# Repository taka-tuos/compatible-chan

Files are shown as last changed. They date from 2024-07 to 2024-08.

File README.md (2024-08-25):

# compatible-chan
[スタックチャン](https://github.com/stack-chan/stack-chan) 用の自由なCoreモジュール (GPLv3)

# ・ _ ・
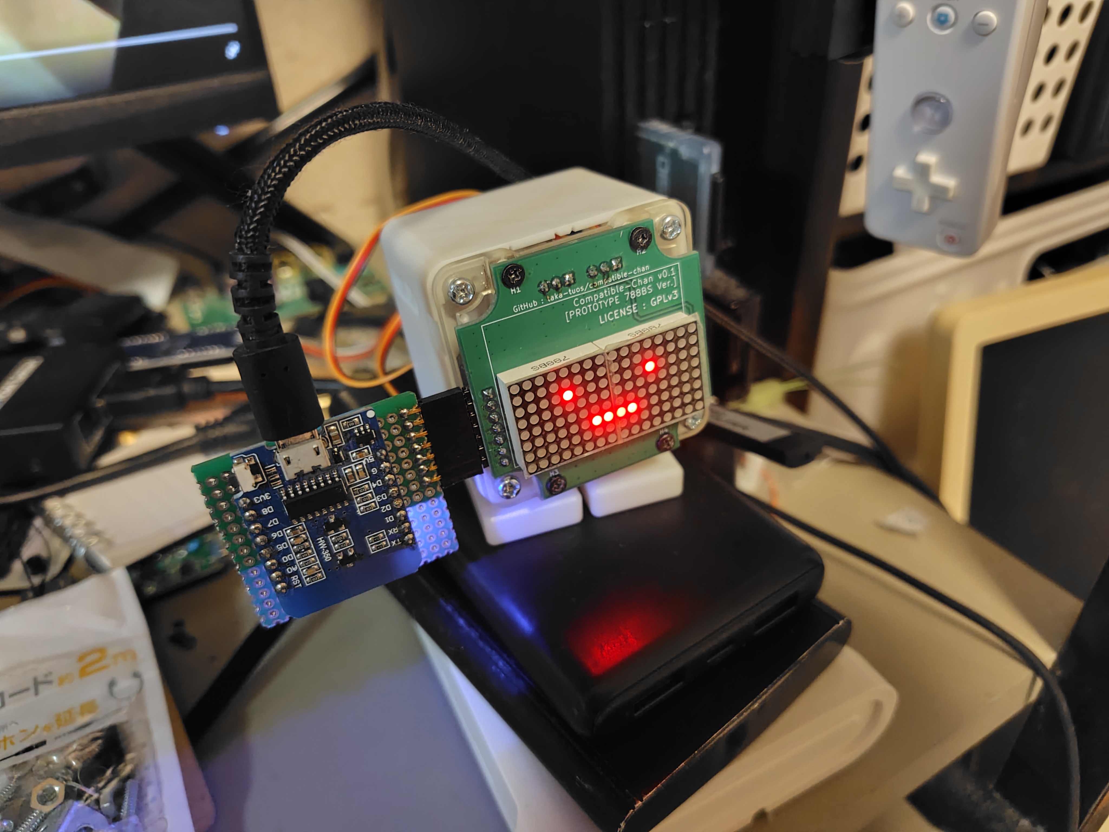
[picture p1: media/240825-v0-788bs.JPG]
v0.1-led 788bs版の動作の様子


# このプロジェクトのスコープ
- スタックチャンのCoreモジュールに自由な選択肢を追加することが目的
- M5Stack系の製品を広範に置き換えるもの**ではない** (スタックチャンに必要な機能のみを実装する)

# FAQ
## Q. M5Stackって「オープンハードウェア」では？
A. 各種ピン仕様や回路図こそオープンではあるが、シェルのCADデータやガーバーファイル、BOM等が公開されていないので「自由」ではない(と自分は考えている)。

## Q. 自由でないと何がダメ？
A. スタックチャンは「サ終とともに死ぬロボットはアカン(意訳)」という思想を含んでいて[^1](https://protopedia.net/prototype/2345)、M5Stackの供給が止まると死ぬ状況はよろしくないはず。  
(実際オンラインに依存していない旧AIBOシリーズでも、部品供給が無いのでバタバタ死んでいる)  
またM5Stackの仕様に縛られる状況でその打開ができないのもよろしくない(よく挙がる例としてはスピーカーとマイクが排他なことなど)

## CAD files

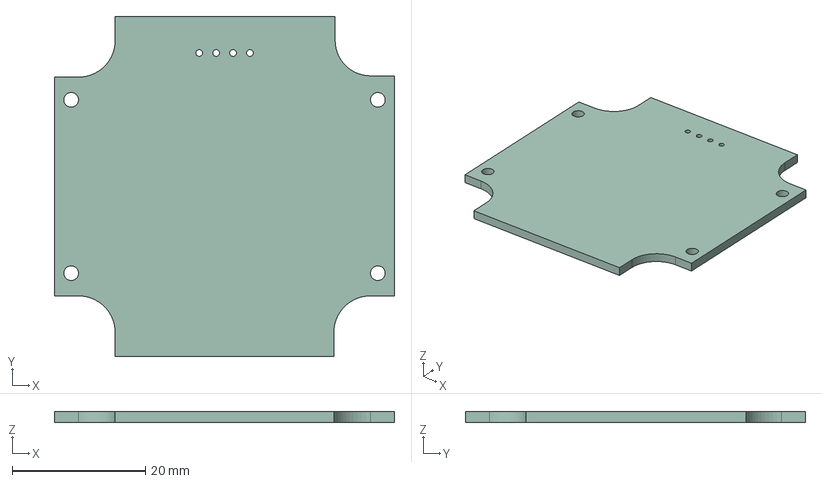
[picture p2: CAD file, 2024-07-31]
compatible-chan-v0/compatible-chan-v0.step
51.0 x 51.0 x 1.60 mm

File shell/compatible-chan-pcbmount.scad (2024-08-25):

use <pcb.scad>

$fn = $preview ? 16 : 48;
m_led = true;

module roundsquare(s, r) {
    union() {
        square(s-r*2, true);
        translate([-(s/2-r),-(s/2-r), 0]) circle(r);
        translate([ (s/2-r),-(s/2-r), 0]) circle(r);
        translate([-(s/2-r), (s/2-r), 0]) circle(r);
        translate([ (s/2-r), (s/2-r), 0]) circle(r);
        translate([-(s/2-r), 0, 0]) square([r*2, s-r*2], true);
        translate([ (s/2-r), 0, 0]) square([r*2, s-r*2], true);
        translate([0,-(s/2-r), 0]) square([s-r*2, r*2], true);
        translate([0, (s/2-r), 0]) square([s-r*2, r*2], true);
    }
}

module outershell(s, r, t, h) {
    linear_extrude(h, convexity = 2) {
        difference() {
            roundsquare(s, r);
            roundsquare(s - t, r - t/2);
        }
    }
}

module screwstand(r1, r2, h, d, b1 = 0, b2 = 0, b3 = 0, b4 = 0) {
    union(){
        linear_extrude(h, convexity = 2) {
            difference() {
                circle(r2);
                circle(r1);
            }
        }
        cylinder(h - d, r2, r2);
        
        difference() {
            union() {
                if(b1 == 1) {
                    translate([-(r2/2), -(r2/2), h / 2]) cube([r2, r2, h], true);
                }
                
                if(b2 == 1) {
                    translate([-(r2/2),  (r2/2), h / 2]) cube([r2, r2, h], true);
                }
                
                if(b3 == 1) {
                    translate([ (r2/2), -(r2/2), h / 2]) cube([r2, r2, h], true);
                }
                
                if(b4 == 1) {
                    translate([ (r2/2),  (r2/2), h / 2]) cube([r2, r2, h], true);
                }
            }
            translate([0, 0, -1]) cylinder(h + 2, r2, r2);
        }
    }
}

union() {
    translate([-(27-5.1),-(27-5.1), 0]) screwstand(2.0, 4.6, 3, 5, 0, 1, 1, 0); 
    translate([-(27-5.1), (27-5.1), 0]) screwstand(2.0, 4.6, 3, 5, 1, 0, 0, 1); 
    translate([ (27-5.1),-(27-5.1), 0]) screwstand(2.0, 4.6, 3, 5, 1, 0, 0, 1); 
    translate([ (27-5.1), (27-5.1), 0]) screwstand(2.0, 4.6, 3, 5, 0, 1, 1, 0); 
    
    translate([-13, -(27-4), 0]) screwstand(1.75, 3.5, 6, 8, 1, 1, 0, 0);
    translate([-13,  (27-4), 0]) screwstand(1.75, 3.5, 6, 8, 1, 1, 0, 0);
    translate([ 13, -(27-4), 0]) screwstand(1.75, 3.5, 6, 8, 0, 0, 1, 1);
    translate([ 13,  (27-4), 0]) screwstand(1.75, 3.5, 6, 8, 0, 0, 1, 1);
    
    linear_extrude(3, convexity = 2) {
        translate([0, -(27-4)]) square([22, 3],true);
        translate([0,  (27-4)]) square([22, 3],true);
        
        translate([-(27-2), 0]) square([3, 35],true);
        translate([ (27-2), 0]) square([3, 35],true);
        
        translate([-(27-9), -(27-4)]) square([3, 7],true);
        translate([-(27-9),  (27-4)]) square([3, 7],true);
        translate([ (27-9), -(27-4)]) square([3, 7],true);
        translate([ (27-9),  (27-4)]) square([3, 7],true);
    }
}

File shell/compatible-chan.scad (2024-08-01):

use <pcb.scad>

$fn = $preview ? 16 : 48;
m_led = true;

module roundsquare(s, r) {
    union() {
        square(s-r*2, true);
        translate([-(s/2-r),-(s/2-r), 0]) circle(r);
        translate([ (s/2-r),-(s/2-r), 0]) circle(r);
        translate([-(s/2-r), (s/2-r), 0]) circle(r);
        translate([ (s/2-r), (s/2-r), 0]) circle(r);
        translate([-(s/2-r), 0, 0]) square([r*2, s-r*2], true);
        translate([ (s/2-r), 0, 0]) square([r*2, s-r*2], true);
        translate([0,-(s/2-r), 0]) square([s-r*2, r*2], true);
        translate([0, (s/2-r), 0]) square([s-r*2, r*2], true);
    }
}

module outershell(s, r, t, h) {
    linear_extrude(h, convexity = 2) {
        difference() {
            roundsquare(s, r);
            roundsquare(s - t, r - t/2);
        }
    }
}

module screwstand(r1, r2, h, d, b1 = 0, b2 = 0, b3 = 0, b4 = 0) {
    union(){
        linear_extrude(h, convexity = 2) {
            difference() {
                circle(r2);
                circle(r1);
            }
        }
        cylinder(h - d, r2, r2);
        
        difference() {
            union() {
                if(b1 == 1) {
                    translate([-(r2/2), -(r2/2), h / 2]) cube([r2, r2, h], true);
                }
                
                if(b2 == 1) {
                    translate([-(r2/2),  (r2/2), h / 2]) cube([r2, r2, h], true);
                }
                
                if(b3 == 1) {
                    translate([ (r2/2), -(r2/2), h / 2]) cube([r2, r2, h], true);
                }
                
                if(b4 == 1) {
                    translate([ (r2/2),  (r2/2), h / 2]) cube([r2, r2, h], true);
                }
            }
            translate([0, 0, -1]) cylinder(h + 2, r2, r2);
        }
    }
}

union() {
    difference() {
        outershell(54, 5, 1.8, 13);
        translate([0, 0, 11.5]) {
            difference() {
                outershell(54-1.4, 5-0.7, 1.8, 2.5);
                cube([54-20, 60, 12], true);
                cube([60, 54-15, 12], true);
            }
        }
        if(!m_led) {
            translate([-10, 0, 10]) {
                cube([60, 35, 25], true);
            }
        }
        translate([0, 0, 7.2+5]) {
            cube([60, 35, 10], true);
        }
    }
    
    translate([-(27-5.1),-(27-5.1), 1.5]) screwstand(2.1, 4.5, 9, 5, 0, 1, 1, 0); 
    translate([-(27-5.1), (27-5.1), 1.5]) screwstand(2.1, 4.5, 9, 5, 1, 0, 0, 1); 
    translate([ (27-5.1),-(27-5.1), 1.5]) screwstand(2.1, 4.5, 9, 5, 1, 0, 0, 1); 
    translate([ (27-5.1), (27-5.1), 1.5]) screwstand(2.1, 4.5, 9, 5, 0, 1, 1, 0); 
    
    translate([-13, -(27-4), 1.5]) screwstand(1.75, 3.5, 5.6, 5, 1, 0, 1, 0);
    translate([-13,  (27-4), 1.5]) screwstand(1.75, 3.5, 5.6, 5, 0, 1, 0, 1);
    
    translate([ 13, -(27-4), 1.5]) screwstand(1.75, 3.5, 5.6, 5, 1, 0, 1, 0);
    translate([ 13,  (27-4), 1.5]) screwstand(1.75, 3.5, 5.6, 5, 0, 1, 0, 1);
    
    if(!m_led) {
        translate([47.8 / 2 - 1.7 + 0.5, 0, 1.5 + 0.5]) cube([1, 36, 1], true);
    }
    
    if($preview) {
        /*translate([0, -2, 2.8]) {
            color("SteelBlue") {
                difference() {
                    translate([0, 0, 0.6]) cube([34, 47, 1.2], true);
                    translate([-(29/2), -(42/2), -2]) cylinder(4, 1.1, 1.1);
                    translate([ (29/2), -(42/2), -2]) cylinder(4, 1.1, 1.1);
                    translate([-(29/2),  (42/2), -2]) cylinder(4, 1.1, 1.1);
                    translate([ (29/2),  (42/2), -2]) cylinder(4, 1.1, 1.1);
                }
            }
            
            color("DarkGray") {
                translate([0, 2.819, -0.75]) cube([28.86, 28.86, 1.8], true);
            }
            
            color("DimGray") {
                translate([0, 0.5, -0.7]) cube([33.9, 37.3, 1.7], true);
            }
            
            color("DimGray") {
                translate([0, 22, 2.54]) cube([10.16, 2.54, 2.54], true);
            }
            
            color("Gold") {
                translate([-1.27     , 22, -1.8+6]) cube([0.6, 0.6, 1.8+1.2+2.54+6], true);
                translate([-1.27-2.54, 22, -1.8+6]) cube([0.6, 0.6, 1.8+1.2+2.54+6], true);
                translate([ 1.27     , 22, -1.8+6]) cube([0.6, 0.6, 1.8+1.2+2.54+6], true);
                translate([ 1.27+2.54, 22, -1.8+6]) cube([0.6, 0.6, 1.8+1.2+2.54+6], true);
            }
        }*/
        
        if(!m_led) {
            translate([-1.7, 0, 1.05 + 1.5]) {
                color("Silver") {
                    translate([0, 0, 0]) cube([47.8, 34.6, 2.05], true);
                }
                
                color("DimGray") {
                    translate([1.7, 0, -0.1]) cube([40.8, 30.6, 2.0], true);
                }
            }
        } else {
            //color("Gray", 0.2) {
                translate([0, 0, 6.6 + 1.6]) {
                    rotate([0, 180, 0]) {
                        //import("compatible-chan-v0-led.stl", convexity = 2);
                        //TXFM_1();
                    }
                }
            //}
        }
    }
    
    //color("DimGray", 0.6) {
        difference() {
            translate([0, 0, 0.3]) linear_extrude(1.2, convexity = 2) roundsquare(54-0.9, 5-0.45);
            if(!m_led) {
                cube([40.8, 30.6, 4], true);
            } else {
                translate([0, -4.6, 0]) cube([41, 20.5, 4], true);
            }
            
            //cube([27.972, 32.634, 4], true);
            //translate([0, 2.819-2, 0]) cube([28.86, 28.86, 4], true);
            //translate([0, 2, 0]) cylinder(4, 16, 16);
            //translate([0, 0, 1.5]) cube([42.04, 27.22, 1.0], true);
        }
    //}
}

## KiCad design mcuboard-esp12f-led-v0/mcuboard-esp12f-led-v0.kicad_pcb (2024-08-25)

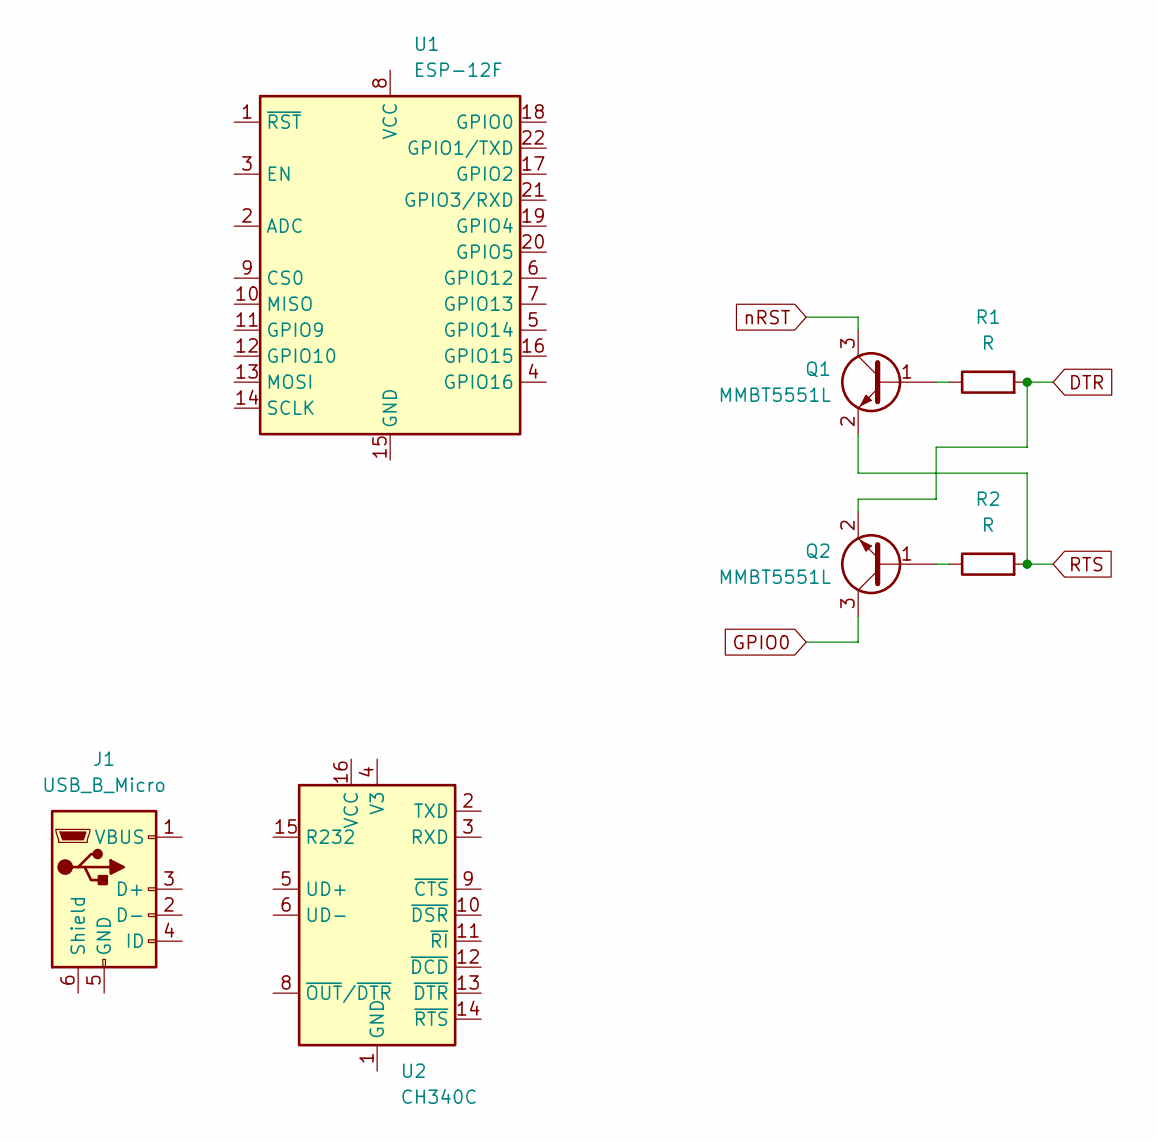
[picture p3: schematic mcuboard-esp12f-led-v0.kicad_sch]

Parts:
J1: USB_B_Micro; USB_Micro-B_Wuerth_629105150521
Q1, Q2: MMBT5551L; SOT-23
R1, R2: R; R_0805_2012Metric_Pad1.20x1.40mm_HandSolder
U1: ESP-12F; ESP-12E
U2: CH340C; SOIC-16_3.9x9.9mm_P1.27mm

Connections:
DTR: Q2.2 (E), R1.2
GPIO0: Q2.3 (C)
unnamed: Q1.1 (B), R1.1
unnamed: Q2.1 (B), R2.1
RTS: Q1.2 (E), R2.2
nRST: Q1.3 (C)

Board: 2 copper layers, 7 parts (0 on the bottom side), 4 nets, no tracks yet.

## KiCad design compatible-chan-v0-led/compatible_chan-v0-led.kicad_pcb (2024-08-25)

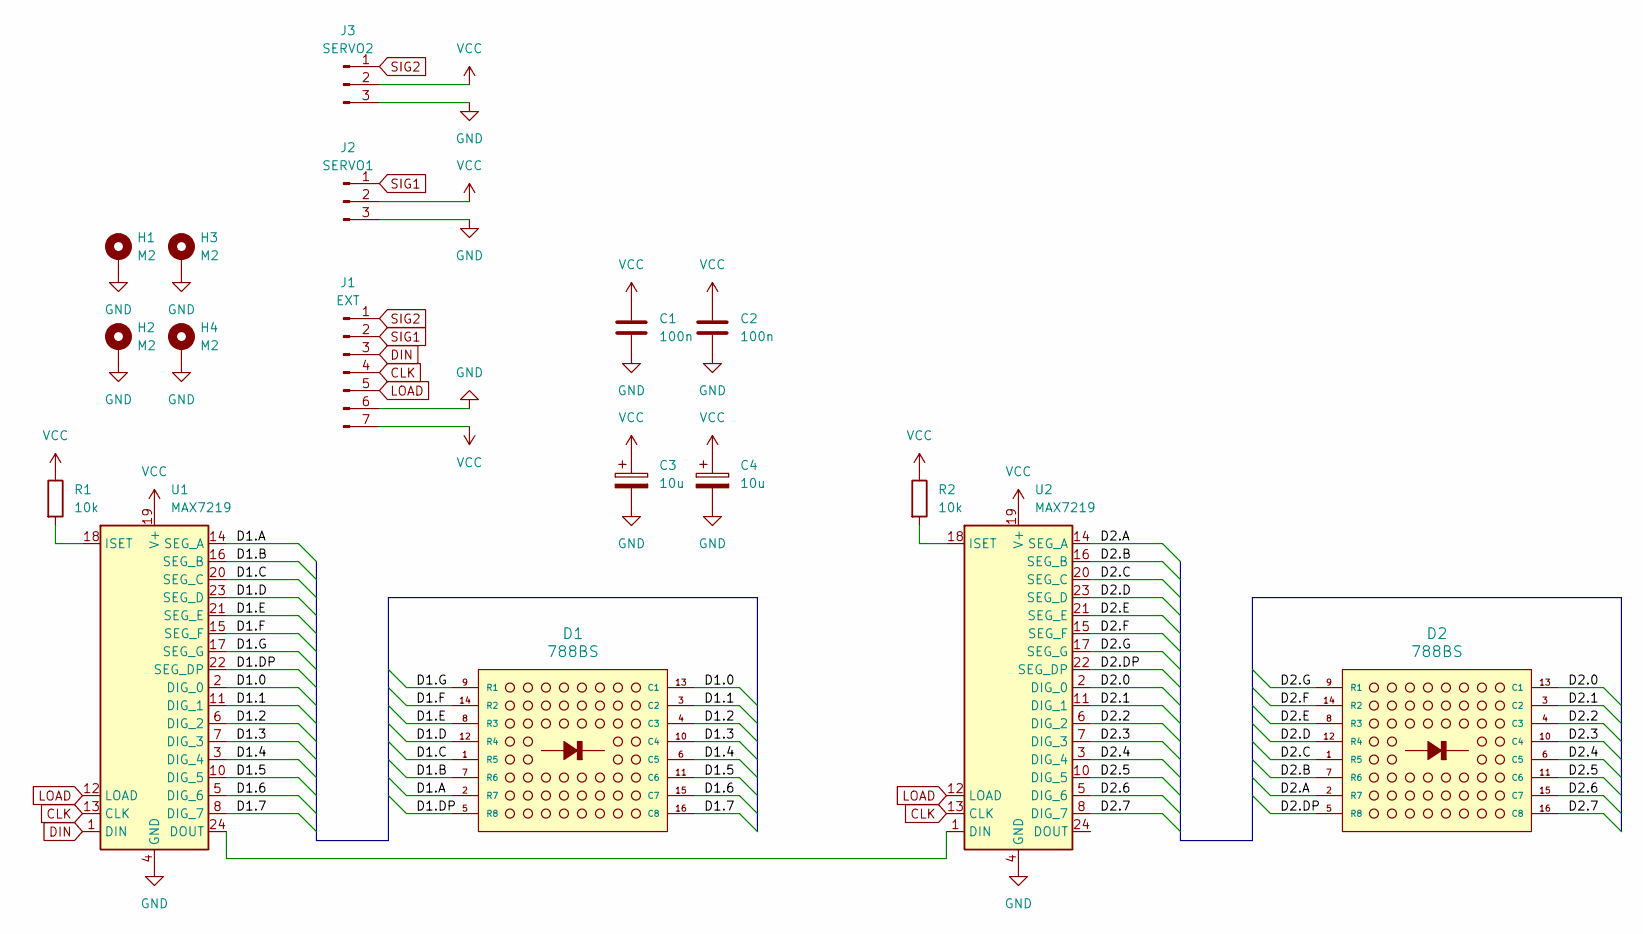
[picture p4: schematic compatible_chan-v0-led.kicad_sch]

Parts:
C1, C2: 100n; C_0805_2012Metric_Pad1.18x1.45mm_HandSolder
C3, C4: 10u; CP_EIA-2012-15_AVX-P_Pad1.30x1.05mm_HandSolder
D1, D2: 788BS; LED_8x8_1.9MM_20x20MM
H1, H2, H3, H4: M2; MountingHole_2.2mm_M2_DIN965_Pad
J1: EXT; PinHeader_1x07_P2.54mm_Horizontal
J2: SERVO1; PinHeader_1x03_P2.54mm_Vertical
J3: SERVO2; PinHeader_1x03_P2.54mm_Vertical
R1, R2: 10k; R_Axial_DIN0207_L6.3mm_D2.5mm_P10.16mm_Horizontal
U1, U2: MAX7219; SOIC-24W_7.5x15.4mm_P1.27mm

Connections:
/D1.0: D1.13 (C1), U1.2 (DIG_0)
/D1.1: D1.3 (C2), U1.11 (DIG_1)
/D1.2: D1.4 (C3), U1.6 (DIG_2)
/D1.3: D1.10 (C4), U1.7 (DIG_3)
/D1.4: D1.6 (C5), U1.3 (DIG_4)
/D1.5: D1.11 (C6), U1.10 (DIG_5)
/D1.6: D1.15 (C7), U1.5 (DIG_6)
/D1.7: D1.16 (C8), U1.8 (DIG_7)
/D1.A: D1.2 (R7), U1.14 (SEG_A)
/D1.B: D1.7 (R6), U1.16 (SEG_B)
/D1.C: D1.1 (R5), U1.20 (SEG_C)
/D1.D: D1.12 (R4), U1.23 (SEG_D)
/D1.DP: D1.5 (R8), U1.22 (SEG_DP)
/D1.E: D1.8 (R3), U1.21 (SEG_E)
/D1.F: D1.14 (R2), U1.15 (SEG_F)
/D1.G: D1.9 (R1), U1.17 (SEG_G)
/D2.0: D2.13 (C1), U2.2 (DIG_0)
/D2.1: D2.3 (C2), U2.11 (DIG_1)
/D2.2: D2.4 (C3), U2.6 (DIG_2)
/D2.3: D2.10 (C4), U2.7 (DIG_3)
/D2.4: D2.6 (C5), U2.3 (DIG_4)
/D2.5: D2.11 (C6), U2.10 (DIG_5)
/D2.6: D2.15 (C7), U2.5 (DIG_6)
/D2.7: D2.16 (C8), U2.8 (DIG_7)
/D2.A: D2.2 (R7), U2.14 (SEG_A)
/D2.B: D2.7 (R6), U2.16 (SEG_B)
/D2.C: D2.1 (R5), U2.20 (SEG_C)
/D2.D: D2.12 (R4), U2.23 (SEG_D)
/D2.DP: D2.5 (R8), U2.22 (SEG_DP)
/D2.E: D2.8 (R3), U2.21 (SEG_E)
/D2.F: D2.14 (R2), U2.15 (SEG_F)
/D2.G: D2.9 (R1), U2.17 (SEG_G)
CLK: J1.4, U1.13 (CLK), U2.13 (CLK)
DIN: J1.3, U1.1 (DIN)
GND: C1.2, C2.2, C3.2, C4.2, H1.1, H2.1, H3.1, H4.1, J1.6, J2.3, J3.3, U1.4 (GND), U1.9 (GND), U2.4 (GND), U2.9 (GND)
LOAD: J1.5, U1.12 (LOAD), U2.12 (LOAD)
unnamed: U1.24 (DOUT), U2.1 (DIN)
unnamed: R1.2, U1.18 (ISET)
unnamed: R2.2, U2.18 (ISET)
SIG1: J1.2, J2.1
SIG2: J1.1, J3.1
VCC: C1.1, C2.1, C3.1, C4.1, J1.7, J2.2, J3.2, R1.1, R2.1, U1.19 (V+), U2.19 (V+)

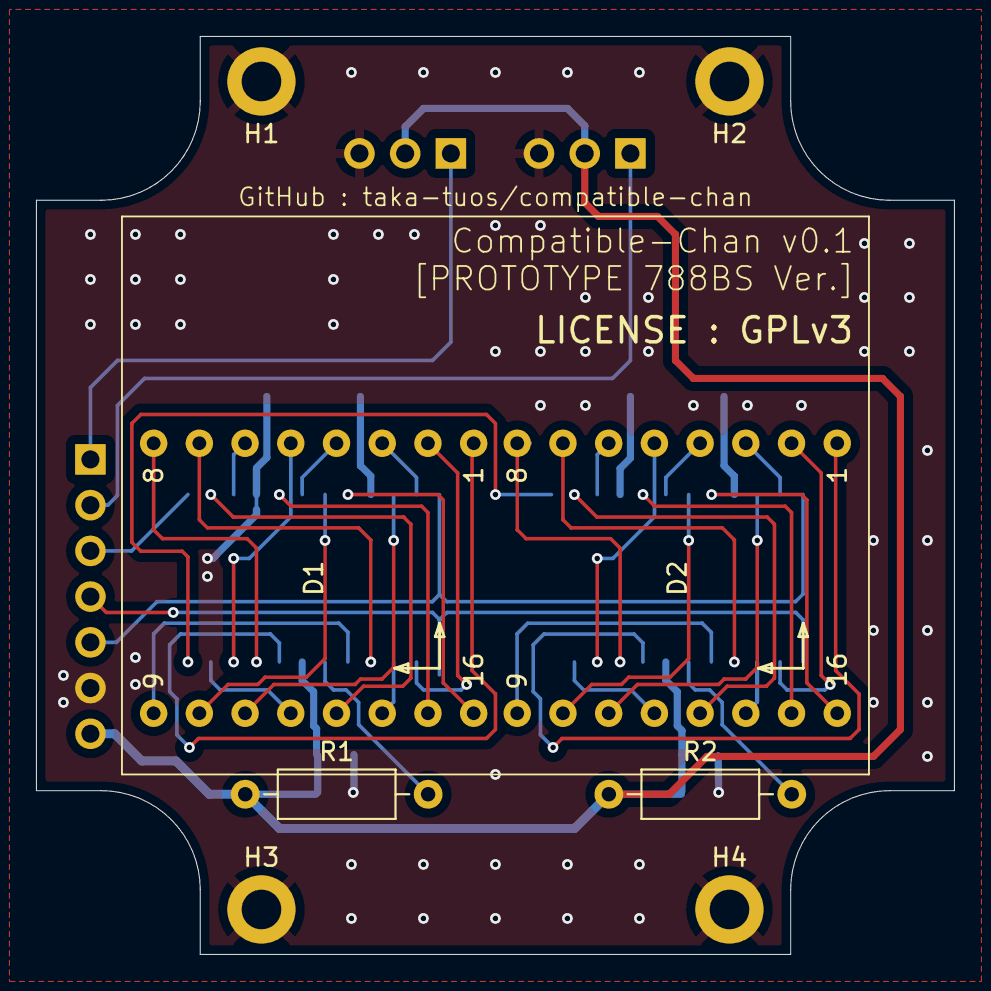
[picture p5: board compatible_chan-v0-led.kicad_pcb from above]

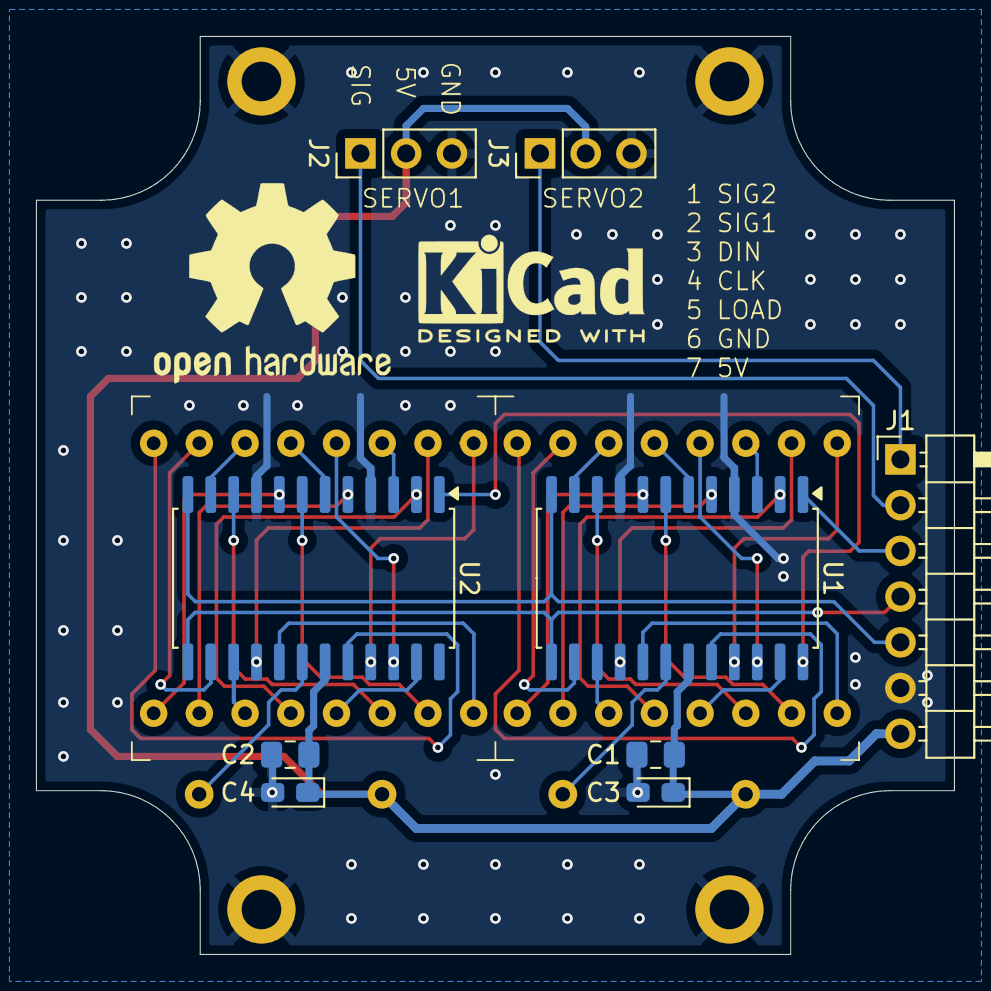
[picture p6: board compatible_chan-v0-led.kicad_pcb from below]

Board: 2 copper layers, 51.0 x 51.0 mm, 17 parts (9 on the bottom side), 42 nets.

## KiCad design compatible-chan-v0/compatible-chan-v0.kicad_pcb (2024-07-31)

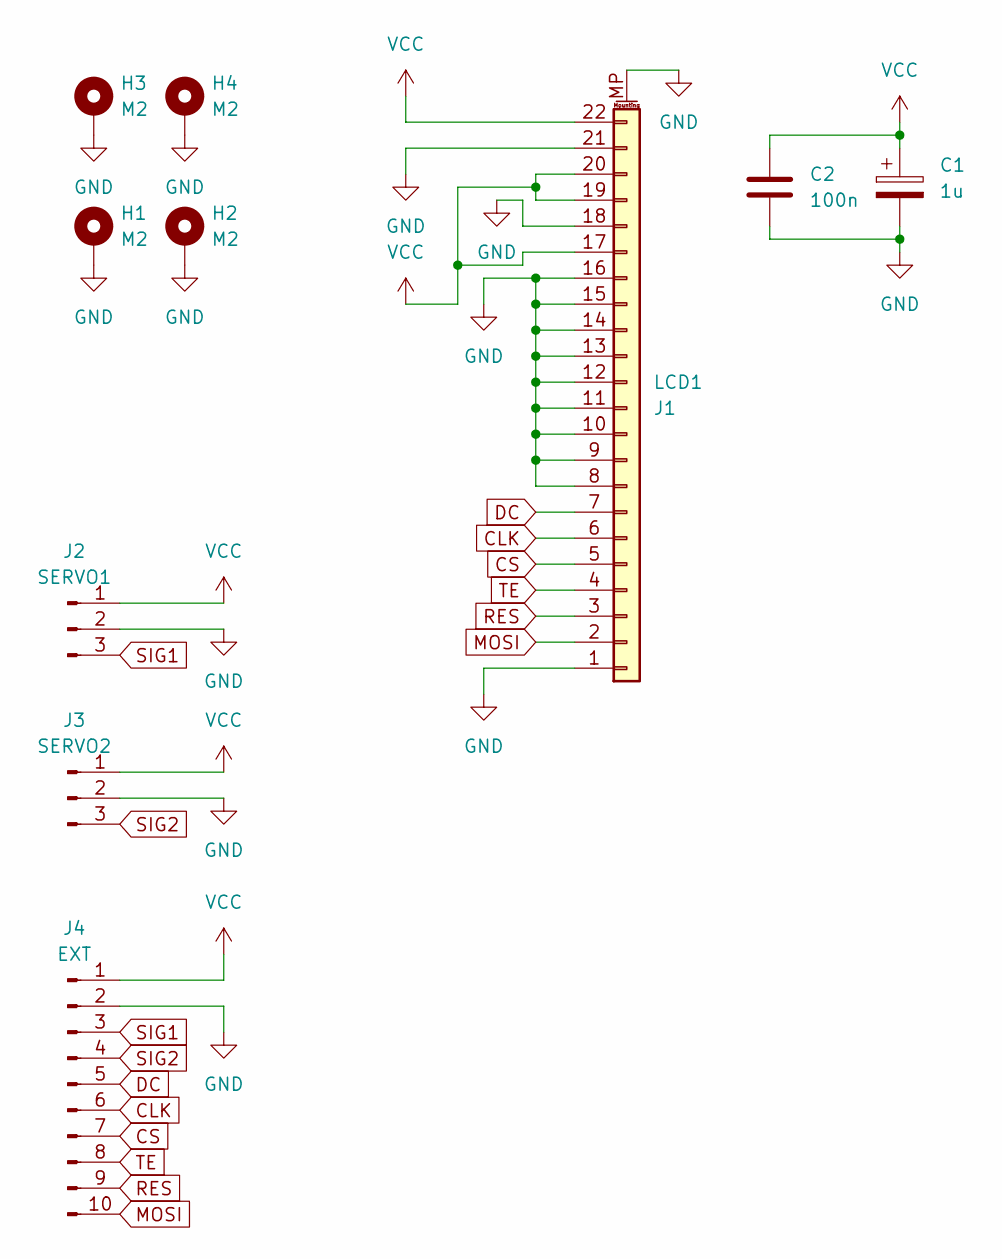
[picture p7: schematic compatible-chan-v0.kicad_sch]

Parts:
C1: 1u; CP_EIA-2012-12_Kemet-R_Pad1.30x1.05mm_HandSolder
C2: 100n; C_0805_2012Metric_Pad1.18x1.45mm_HandSolder
H1, H2, H3, H4: M2; MountingHole_2.2mm_M2_DIN965_Pad
J1: LCD1; TE_2-1734839-2_1x22-1MP_P0.5mm_Horizontal
J2: SERVO1; PinHeader_1x03_P2.54mm_Vertical
J3: SERVO2; PinHeader_1x03_P2.54mm_Vertical
J4: EXT; PinHeader_1x10_P2.54mm_Horizontal

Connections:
CLK: J1.6, J4.6
CS: J1.5, J4.7
DC: J1.7, J4.5
GND: C1.2, C2.2, H1.1, H2.1, H3.1, H4.1, J1.1, J1.8, J1.9, J1.10, J1.11, J1.12, J1.13, J1.14, J1.15, J1.16, J1.18, J1.21, J1.MP (MountPin), J2.2, J3.2, J4.2
MOSI: J1.2, J4.10
RES: J1.3, J4.9
SIG1: J2.3, J4.3
SIG2: J3.3, J4.4
TE: J1.4, J4.8
VCC: C1.1, C2.1, J1.17, J1.19, J1.20, J1.22, J2.1, J3.1, J4.1

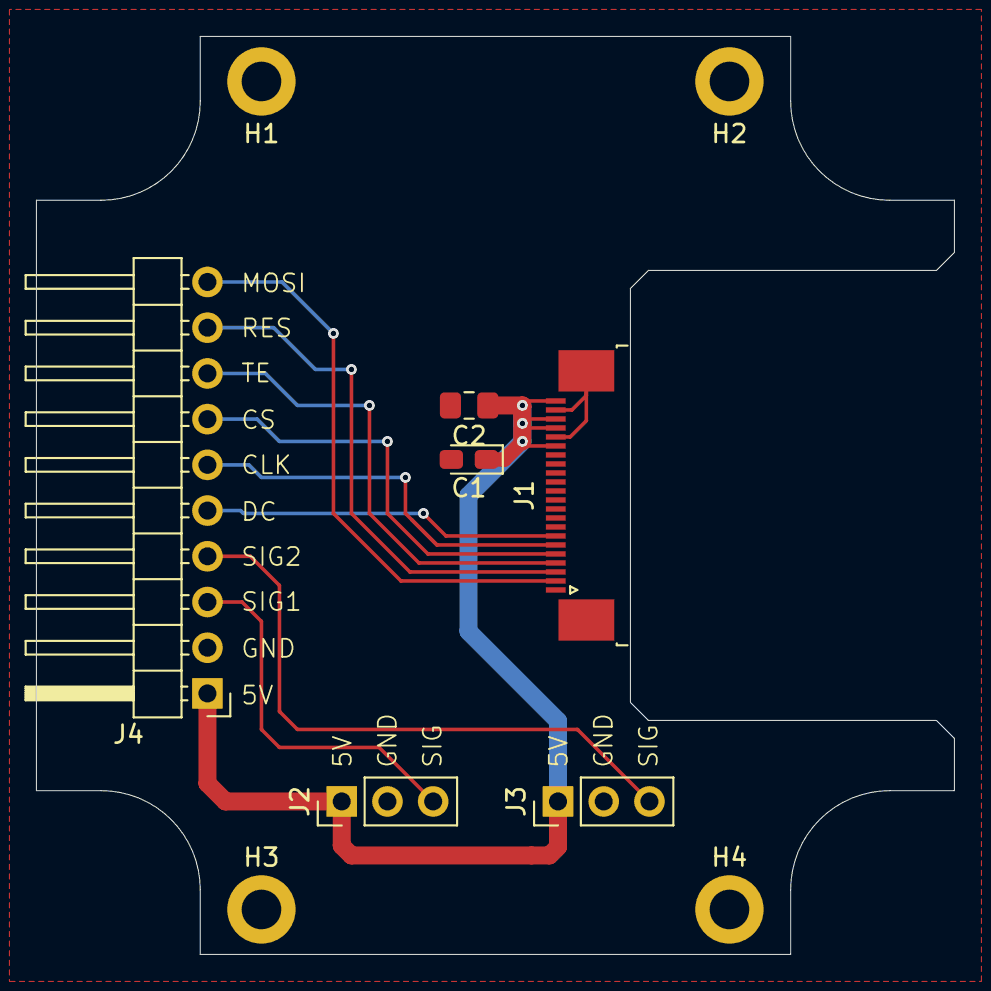
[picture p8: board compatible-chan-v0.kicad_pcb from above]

Board: 2 copper layers, 51.0 x 51.0 mm, 10 parts (0 on the bottom side), 10 nets.

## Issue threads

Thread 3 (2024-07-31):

v0 - 外装

taka-tuos, 2024-07-31:
# 共通事項
- [x] M5Stack規格の共通部分
- [ ] インサート穴調整

# その他
- [x] ST7789用部分
- [ ] LEDマトリクス用部分

taka-tuos, 2024-08-01:
LED用部分:[331cef1](https://github.com/taka-tuos/compatible-chan/commit/331cef1364ccf1515b8460b07844a3fe2083663a)

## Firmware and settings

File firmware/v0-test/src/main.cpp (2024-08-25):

#include <Arduino.h>

#include <MD_MAX72xx.h>

#define HARDWARE_TYPE MD_MAX72XX::FC16_HW
#define MAX_DEVICES  2

#define CLK_PIN   13  // or SCK
#define DATA_PIN  12  // or MOSI
#define CS_PIN    15  // or SS

#include <Servo.h>

Servo myservo1;
Servo myservo2;

MD_MAX72XX mx = MD_MAX72XX(HARDWARE_TYPE, DATA_PIN, CLK_PIN, CS_PIN, MAX_DEVICES);

void setup() {
  myservo1.attach(2);
  myservo2.attach(0);
  
  myservo1.write(90);// move servos to 90°
  myservo2.write(90);// move servos to 90°
  delay(2000);  
  
  mx.begin();

  mx.setRow(0,0,0b00000100);
  mx.setRow(0,1,0b00000100);
  mx.setRow(0,2,0b00000000);
  mx.setRow(0,3,0b00100000);
  mx.setRow(0,4,0b00000000);
  mx.setRow(0,5,0b00000000);
  mx.setRow(0,6,0b00000000);
  mx.setRow(0,7,0b00000000);

  mx.setRow(1,0,0b00000000);
  mx.setRow(1,1,0b00000000);
  mx.setRow(1,2,0b00000000);
  mx.setRow(1,3,0b00000000);
  mx.setRow(1,4,0b00100000);
  mx.setRow(1,5,0b00000000);
  mx.setRow(1,6,0b00000100);
  mx.setRow(1,7,0b00000100);
}

void loop() {
  double rad1 = (double)(millis() % 10100) / 10100.0 * 2 * PI;
  double rad2 = (double)(millis() % 7100) / 7100.0 * 2 * PI;

  myservo1.write(90 + (sin(rad1) * 20.0));
  myservo2.write(90 + (cos(rad2) * 10.0 - 10.0));
}

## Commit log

2024-07-31 first commit, v0基板etc追加
    [compatible-chan-v0.kicad_pcb, compatible-chan-v0.kicad_sch, compatible-chan-v0.step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]
2024-07-31 README更新 Current Status削除
2024-08-01 LED版関連更新 基板更新,シェル設計
    [compatible-chan.scad, compatible_chan-v0-led.kicad_pcb, compatible_chan-v0-led.kicad_sch]
2024-08-01 READMEの文面を調整
2024-08-01 LED版調整 (#3) インサート穴再調整、フロント穴作成
    [compatible-chan.scad]
2024-08-25 v0-led基板更新、テストファーム・v0.1用MCU基板追加
    [compatible-chan-pcbmount.scad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]
2024-08-25 README更新
2024-08-25 ファームウェア更新

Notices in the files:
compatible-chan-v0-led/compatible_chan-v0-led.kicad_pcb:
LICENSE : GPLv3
